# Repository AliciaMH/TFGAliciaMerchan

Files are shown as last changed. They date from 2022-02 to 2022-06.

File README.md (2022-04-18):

# TFGAliciaMerchan

# Carpeta: Excel Proyecto:

Aquí se encuentran todos los archivos de excel relacionados con el proyecto:
1) "CalculadoraErrorTiempo" : Para que las personas que quieran realizar el experimento puedan tener el valor exacto del error del tiempo para el recorrido que deseen y     a la velocidad que deseen. Sólo tendrán que introducir los parámetros iniciales (ángulo final, inicial y velocidad angular) y se calculará automáticamente el error.     Además, se proporciona como extra la información de la velocidad lineal a la que hará el experimento y la opción de obtener una gráfica como las anteriores en las       que según el ángulo inicial y la velocidad angular constante se puede obte-ner cómo variará el error según el ángulo final.

2) "VelocidadesAngulares_SimuladorGeologicoAlicia" : Aqui se recogen los datos principales del proyecto:
         Hojas:
         a) cálculos: contiene los cálculos para cada velocidad angular dada con las condiciones del motor usado, tiempo de espera necesario, etc
         b) Calculadora de error: es la misma que la del punto 1, por si se prefiere tenerlo todo junto en un único excel
         c) Velocidades medias: Cálculo de las velocidades lineales medias para cada velocidad angular (necesario para la hoja a)
         d) Linealización: Permite ver la correspondencia de los ángulos con la distancia recorrida por la bisagra especial. También hay una linealización que se comenta             en la memoria del TFG pero que al final no es necesaria ya que se realiza el cambio directo. 
         e) Error: Esta hoja se utilizó para la primera aproximación que se quería realizar, sin embargo, al final no fue la aproximación elegida asique se puede obviar.
         
# Carpeta: código final Arduino prueba casa
Aquí se encuentran el excel con los parámentros necesarios para hacer la simulación en casa con otro motor distinto, los csv con los vectores necesarios para el código de arduino y el propio código de arduino. El archivo de arduino que contiene un -10 en el nombre es el que se usó de prueba para establecer el sensor de inicio de carrera en un lugar distinto al 0.

# Carpeta: simulación SAM

Aquí se encuetra la simulación final con las medidas correspondientes del proyecto en un archivo .SAM para abrir en el programa y por otro lado el excel con los datos obtenidos de la simulación y la comparativa con los otros métodos.

# Carpeta: bisagra principal

Recoge algunos de los diseños para la bisagra principal realizados en freeCAD

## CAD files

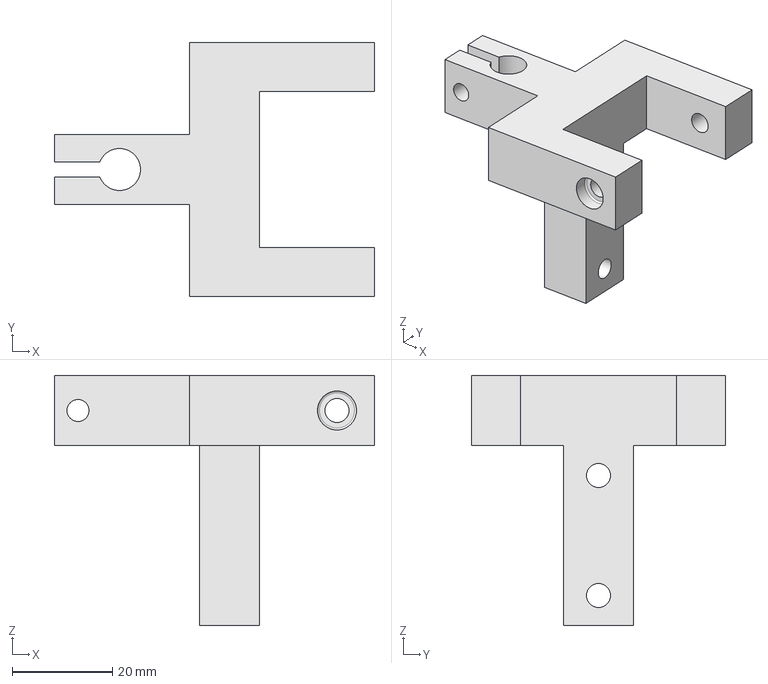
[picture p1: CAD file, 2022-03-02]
Bisagra Principal/ElementoUnionPerfil30mmEje8mm.FCStd
64.0 x 50.8 x 50.0 mm

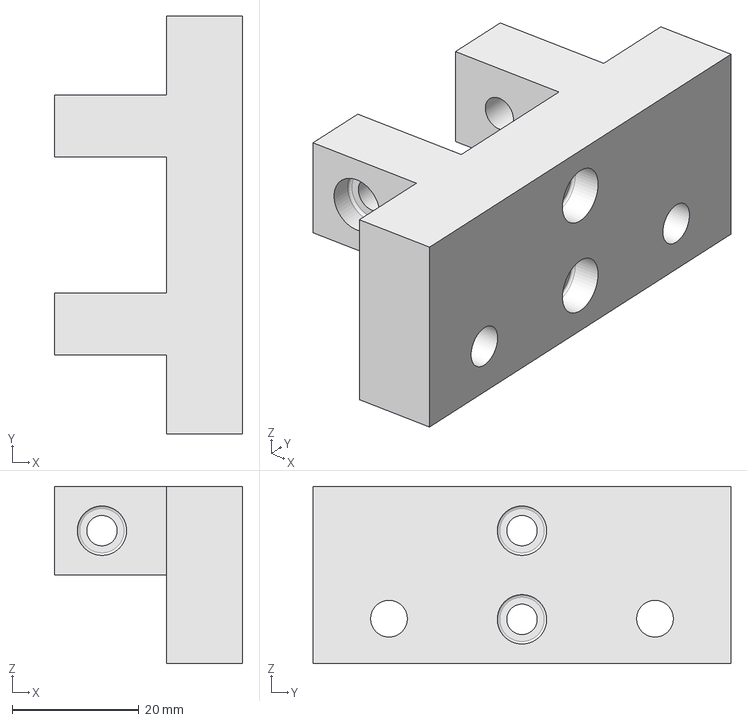
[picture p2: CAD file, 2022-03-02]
Bisagra Principal/ElementoUnionPerfil20mmPillowBlock8mm.FCStd
29.7 x 66.0 x 28.0 mm

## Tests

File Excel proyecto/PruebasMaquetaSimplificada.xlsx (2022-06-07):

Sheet: Hoja1
PRUEBA CON MAQUETA SIMPLIFICADA CASA
Prueba | a | b | c | d | e | f | g | h | i | j | k
θinicial (°) | 1 | 0 | 2 | 0 | 0 | 0 | 1.5 | 3 | -1 | 0 | 0
θfinal (°) | 3 | 3 | 6 | 1 | 5 | 1.5 | 7 | 6 | 4 | 8 | 7.5
ω (°/h) | 8 | 8.8 | 6 | 3 | 9.9 | 1.5 | 7 | 3 | 6.5 | 8.5 | 9
Avance
a_sim (mm) | 24.47 | 36.69 | 49.13 | 12.22 | 61.25 | 18.33 | 67.62 | 36.89 | 61.17 | 98.39 | 92.17
a_teo (mm) | 24.47 | 36.69 | 49.13 | 12.22 | 61.24 | 18.33 | 67.62 | 36.89 | 61.17 | 98.38 | 92.16
error (%) | 0.01 | 0.01 | 0.004070998209 | 0.02 | 0.01 | 0.00 | 0.001478874281 | 0.01 | 0.004391544475 | 0.01 | 0.01
Tiempo(h)
t_sim (h) | 0.243 | 0.321 | 0.640 | 0.292 | 0.481 | 0.906 | 0.768 | 0.958 | 0.746 | 0.906 | 0.796
t_aprox (h) | 0.242 | 0.330 | 0.648 | 0.323 | 0.490 | 0.968 | 0.765 | 0.974 | 0.745 | 0.917 | 0.811
t_teo (h) | 0.250 | 0.341 | 0.667 | 0.333 | 0.505 | 1.000 | 0.786 | 1 | 0.769 | 0.941 | 0.833
error (%) | -0.550 | 2.862 | 1.277 | 9.615 | 1.814 | 6.365 | -0.399 | 1.669 | -0.042 | 1.112 | 1.802
error absoluto | -0.001 | 0.009 | 0.008 | 0.031 | 0.009 | 0.062 | -0.003 | 0.016 | -0.0003153086918 | 0.010 | 0.015
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

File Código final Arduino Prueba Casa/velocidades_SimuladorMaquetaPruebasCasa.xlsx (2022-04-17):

 |  |  |  |  |  |  |  |  | TEORICO | EL QUE VAMOS A DAR
wdado(grados/h) | v (cm/h) | v (mm/h) | v (μm/s) | medio paso/s | s/medio paso | ms / medio paso | us / medio paso | t_mediomicropaso (ms) | t_mediomicropaso (us) | t_mediomicropaso (us) | t_espera (us)
0 | 0.0000 | 0 | 0 | 0 | 0 | 0.00 | 0.00 | 0.000 | 0.00 | 0 | 0.00
0.1 | 0.1263 | 1.262727836 | 0.351 | 0.140 | 7.127 | 7127.43 | 7127426.63 | 222.732 | 222732.08 | 100 | 7124226.63 | Pasos por vuelta = | 200 | VELOCIDAD MINIMA
0.2 | 0.2525 | 2.525455672 | 0.702 | 0.281 | 3.564 | 3563.71 | 3563713.31 | 111.366 | 111366.04 | 100 | 3560513.31 | Reduccion = | 1
0.3 | 0.3788 | 3.788183507 | 1.052 | 0.421 | 2.376 | 2375.81 | 2375808.88 | 74.244 | 74244.03 | 100 | 2372608.88 | Pasos / vuelta = | 200 | PPS1/2 = | 150
0.4 | 0.5051 | 5.050911343 | 1.403 | 0.561 | 1.782 | 1781.86 | 1781856.66 | 55.683 | 55683.02 | 100 | 1778656.66 | Avance / vuelta (mm) = | 1 | vmin (μm/s) = | 375.000
0.5 | 0.6314 | 6.313639179 | 1.754 | 0.702 | 1.425 | 1425.49 | 1425485.33 | 44.546 | 44546.42 | 100 | 1422285.33 | Avance / paso (mm) = | 0.005 | vmin (cm/h) = | 135.000
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

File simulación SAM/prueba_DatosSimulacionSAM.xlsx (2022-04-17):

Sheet: Datos sam maqueta actual(9 grad
Result listing SAM 6.1.46 . Mechanism: Modelo final
________________________________________________________________________ |  |  |  |  | unidades corregidas |  | velocidad lineal husillo |  | Distancia real considernado el 0 en 0 grados |  |  | Velocidad angular placa
Nr: | A(1) | Vy(2) | y(2) | AV(1) | A(1) | Vy(2) | Vy(2) | y(2) | Y_0(2) | Y_0(2) | AV(1) | AV(1) |  | Vy(2)_SAM | Vy(2)_Formula | Vy(2)_RadReal | Vy(2)_const | Error SAM/Formula
[-] | [deg] | [mm/s] | [mm] | [deg/s] | [deg] | [mm/s] | [cm/h] | [mm] | [mm] | [cm] | [deg/s] | [deg/h] |  | [cm/h] | [cm/h] | [cm/h] | [cm/h] | [cm/h]
0 | 0 | 27.15 | 300000 | 2.222 | 0 | 0.02715 | 9.7740 | 300 | 0 | 0 | 0.002222 | 7.9992 |  | 9.7740 | 9.7729 | 9.7738 | 9.93388853 | 0.0011
1 | 1000 | 27.16 | 312200 | 2.222 | 1 | 0.02716 | 9.7776 | 312.2 | 12.2 | 1.22 | 0.002222 | 7.9992 |  | 9.7776 | 9.7758 | 9.7753 | 9.93388853 | 0.0018
2 | 2000 | 27.18 | 324400 | 2.222 | 2 | 0.02718 | 9.7848 | 324.4 | 24.4 | 2.44 | 0.002222 | 7.9992 |  | 9.7848 | 9.7848 | 9.7798 | 9.93388853 | 1.595213334e-05
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

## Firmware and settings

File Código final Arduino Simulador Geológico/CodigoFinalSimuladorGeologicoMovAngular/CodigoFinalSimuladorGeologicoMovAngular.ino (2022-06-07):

//CÓDIGO FINAL ARDUINO PARA SIMULACIÓN GEOLÓGICA CON MOVIMIENTO ANGULAR//Falta cambiar los vectores y la sensibilidad

#include <TimerOne.h>       // Libreria del timer 1
#include <TimerThree.h>     // Libreria del timer 3
#include <TimerFour.h>      // Libreria del timer 4

#include <LiquidCrystal.h>  // Libreria de la pantalla LCD
LiquidCrystal lcd(16, 17, 23, 25, 27, 29);

//Pines de la shield
#define LCD_PINS_RS 16      // LCD control conectado a GADGETS3D  shield LCDRS
#define LCD_PINS_ENABLE 17  // LCD enable pin conectado a GADGETS3D shield LCDE
#define LCD_PINS_D4 23      // LCD signal pin, conectado a GADGETS3D shield LCD4
#define LCD_PINS_D5 25      // LCD signal pin, conectado a GADGETS3D shield LCD5
#define LCD_PINS_D6 27      // LCD signal pin, conectado a GADGETS3D shield LCD6
#define LCD_PINS_D7 29      // LCD signal pin, conectado a GADGETS3D shield LCD7
#define X_MIN_PIN 3         // PIN para el fin de carrera colocado al inicio del recorrido (1: presionado (true))
#define X_MAX_PIN 2         // PIN para el fin de carrera colocado al inicio del recorrido (1: presionado (true))

#define X_STEP_PIN 54       // PIN de los pasos del controlador DRV8825 del motor paso a paso
#define X_DIR_PIN 55        // PIN de la direccion del controlador DRV8825 del motor paso a paso
#define X_ENABLE_PIN 38     // PIN del enable del controlador DRV8825 del motor paso a paso

#define BTN_EN1 31          // Encoder, conectado a GADGETS3D shield S_E1
#define BTN_EN2 33          // Encoder, cconectado a GADGETS3D shield S_E2
#define BTN_ENC 35          // Encoder Click, connected to Gadgets3D shield S_EC

// VARIABLES MEDIDA POSICION

bool fc_inic_X = true;      // Valor del final de carrera situacion al inicio del experimento
bool fc_fin_X = true;       // Valor del final de carrera situacion al final del experimento

const float L = 254.78;     // Corresponde a la distancia máxima, es decir, cuando el ángulo es 20 grados
float LMin = -123.429;      // Corresponde a la distancia mínima, es decir, cuando el ángulo es -10 grados. Corresponde además al lugar dónde irá colocado el sensor inicio de carrera
int Lb = 700;               // Longitud entre la bisagra especial y la bisagra principal
const float pi = 3.14159265;// pi number
int AMax = 20;              // Ángulo máximo que se puede llevar a cabo
int AMin = -10;             // Ángulo minimo que se puede llevar a cabo

// VARIABLES MEDIDA TIEMPO 

int horas = 0;              // Variable que cuenta las horas del experimento
int minutos = 0;            // Variable que cuenta los minutos del experimento
volatile int segundos = 0;  // Variable que cuenta los segundos del experimento

// VARIABLES MOVIMIENTO MOTOR

unsigned long t_mediomicropaso = 0;   // Variable en la que introducimo el tiempo de cada medio micropaso
unsigned long t_mediopaso = 0;        // Variable en la que introducimo el tiempo de cada medio paso
int v = 1;                            // Velocidad del sistema
int Vmax = 100;                        // Posición 100 de los vectores de medio paso y micro paso(1000 cm/h)
int posicion = 0;                     //Cogerá v si estoy en el experimento normal o Vmax si estoy yendo a 0
volatile int nivel = LOW;             // Nivel del motor paso a paso
unsigned long micropasos = 0;         // Numero de micropasos dados
unsigned long n_mediospasos = 0;      // Numero de medios pasos cuando el experimento empieza en 0 mm
volatile int n_mediospasos2 = 0;      // Numero de medios pasos cuando el experimento no empieza en 0 mm
float avance_mediospasos = 0;         // Avance a partir de los medios pasos dados por el motor conocido su avance por cada medio paso cuando el experimento empieza en 0 mm
float avance_mediospasos2 = 0;        // Avance a partir de los medios pasos dados por el motor conocido su avance por cada medio paso cuando el experimento no empieza en 0 mm
float di_X, df_X = 0;                 // Distancia inicial y final que queremos en el experimento. Lo he cambiado por float para que pueda tener decimales
float ang_i, ang_f = 0;               // Ánulos iniciales, será lo que elija el usuario en este experimento
float rad, radf, radMin=0;            // Variable para pasar el número de grados a radianes para poder utilizar la tangente

// El siguiente vector muestra los tiempos de cada medio micropaso dependiendo de la velocidad seleccionado. Este vector se encuentra en un .csv en el GitHub del autor del trabajo
// El último elemento corresponde a la mayor velocidad que puede alcanzar para que pueda ir hasta el ángulo inicial indicado a una velocidad mayor
float vectort_mediomicropaso[] = {0,78,78,78,78,78,78,78,78,78,78,78,78,78,78,78,78,78,78,78,78,78,78,78,78,78,78,78,78,78,78,78,78,78,78,78,78,78,78,78,78,78,78,78,78,78,78,78,78,78,78,78,78,78,78,78,78,78,76.80416624,75.50240071,74.24402737,73.02691216,71.84905874,70.70859749,69.60377566,68.53294834,67.49457033,66.48718869,65.50943591,64.5600238,63.63773774,62.74143158,61.87002281,61.02248825,60.19786003,59.39522189,58.61370582,57.85248886,57.11079028,56.38786889,55.68302053,54.99557583,54.32489807,53.67038123,53.03144812,52.40754873,51.79815863,51.20277749,50.62092775,50.05215328,49.49601824,48.95210596,48.42001785,47.89937249,47.3898047,46.89096465,46.4025171,45.92414064,45.45552696,44.99638022,28.39};

// El siguiente vector muestra los tiempos de cada medio paso dependiendo de la velocidad seleccionado. Este vector se encuentra en un .csv en el GitHub del autor del trabajo
// El último elemento corresponde a la mayor velocidad que puede alcanzar para que pueda ir hasta el ángulo inicial indicado a una velocidad mayor
float vectort_mediopaso[] = {0,142548.5325,71274.26627,47516.17751,35637.13314,28509.70651,23758.08876,20364.07608,17818.56657,15838.72584,14254.85325,12958.9575,11879.04438,10965.27173,10182.03804,9503.235503,8909.283284,8385.207797,7919.362919,7502.554344,7127.426627,6788.025359,6479.478752,6197.762285,5939.522189,5701.941302,5482.635867,5279.575279,5091.019019,4915.466639,4751.617751,4598.339759,4454.641642,4319.652501,4192.603898,4072.815216,3959.68146,3852.663042,3751.277172,3655.090578,3563.713314,3476.793477,3394.01268,3315.082152,3239.739376,3167.745168,3098.881142,3032.947501,2969.761095,2909.153725,2850.970651,2795.069266,2741.317934,2689.594954,2639.78764,2591.791501,2545.50951,2500.851448,2457.73332,2416.076823,2375.808876,2336.861189,2299.16988,2262.67512,2227.320821,2193.054347,2159.826251,2127.590038,2096.301949,2065.920762,2036.407608,2007.72581,1979.84073,1952.719624,1926.331521,1900.647101,1875.638586,1851.279643,1827.545289,1804.411804,1781.856657,1759.858426,1738.396738,1717.452199,1697.00634,1677.041559,1657.541076,1638.48888,1619.869688,1601.668905,1583.872584,1566.467391,1549.440571,1532.77992,1516.47375,1500.510869,1484.880547,1469.5725,1454.576863,1439.884167,908.63};


// VARIABLES MAQUINA DE ESTADOS

int inicio = 0;                       // Variable que inicia el experimento cuando comienza en el sensor de principio de carrera
int inicio_experimento = 0;           // Variable que inicia el experimento cuando comienza en di_X mm
int inicio_contadortiempo = 0;       // Variable que inicia el experimento cuando no comienza en 0 mm
int fin = 0;                          // Variable que para el experimento cuando llega al final de carrera 
int volatile estado = 0;              // Variables del estado


// VARIABLES LCD

int fila, columna = 0;                                             // Variable de fila y columna en la pantalla lcd
bool btn_en1, btn_en2, btn_enc, btn_en1_prev, btn_en2_prev ;       // Variables de lectura directa del codificador giratorio mecanico
bool direccion = false;                                            // Direccion del codificador
bool derecha, izquierda, pulsador = false;                         // Variables de lectura del codificador interpretadas
int i = 0;                                                         // Contador de pulsos

// SIGNOS CREADOS

byte empty[8] =
{
  B00000,
  B00100,
  B01010,
  B10001,
  B10001,
  B01010,
  B00100,
};
byte full[8] =
{
  B00000,
  B00100,
  B01110,
  B11111,
  B11111,
  B01110,
  B00100,
};
byte micro[8] =
{
  B00000,
  B10001,
  B10001,
  B11011,
  B10101,
  B10000,
  B10000,
};
byte arrow[8] =
{
  B00000,
  B00001,
  B00001,
  B00001,
  B01001,
  B11111,
  B01000,
};

void setup() {

  pinMode(BTN_EN1, INPUT_PULLUP);     // Encoder 1
  pinMode(BTN_EN2, INPUT_PULLUP);     // Encoder 2
  pinMode(BTN_ENC, INPUT_PULLUP);     // Encoder Swith
  
  pinMode(X_MIN_PIN, INPUT_PULLUP);   // Fin de carrera inicio  
  pinMode(X_MAX_PIN, INPUT_PULLUP);   // Fin de carrera final           

  lcd.begin(20, 4);   // 20 columnas y 4 filas

  pinMode(X_STEP_PIN , OUTPUT);
  pinMode(X_DIR_PIN , OUTPUT);
  pinMode(X_ENABLE_PIN , OUTPUT);

  btn_en1 , btn_en1_prev = digitalRead(BTN_EN1);
  btn_en2 , btn_en2_prev = digitalRead(BTN_EN2);
  btn_enc = digitalRead(BTN_ENC);

  lcd.createChar(0, empty);   // 0: numero de carácter; empty: matriz que contiene los pixeles del carácter
  lcd.createChar(1, full);    // 1: numero de carácter; full: matriz que contiene los pixeles del carácter
  lcd.createChar(2, micro);   // 2: numero de carácter; micro: matriz que contiene los pixeles del carácter
  lcd.createChar(3, arrow);   // 3: número de carácter; arrow: matriz que contiene los pixeles del carácter
 
  digitalWrite(X_ENABLE_PIN , LOW);         // Habilitación a nivel bajo del motor paso a paso

  Timer3.initialize(1000000);              // Inicialización de la interrupcion del contador de segundos
  Timer3.attachInterrupt(Temporizador);    // Función de la interrupcion del contador de segundos
  
}

////////////////// PROCESOS ENCODER /////////////////////

void leer_encoder()
{
  btn_en1 = digitalRead(BTN_EN1);
  btn_en2 = digitalRead(BTN_EN2);
  digitalWrite(X_DIR_PIN, direccion);

  if (btn_en1 != btn_en1_prev || btn_en2 != btn_en2_prev)
  {
    if (btn_en2 == false & btn_en1 == false & btn_en2_prev == true & btn_en1_prev == false)
    {
      derecha = true;
      izquierda = false;
    }
    else if ( btn_en2 == false & btn_en1 == false & btn_en2_prev == false & btn_en1_prev == true )
    {
      derecha = false;
      izquierda = true;
    }
    else
    {
      derecha = false;
      izquierda = false;
    }
  }
  else
  {
    derecha = false;
    izquierda = false;
  }
  btn_en1_prev = btn_en1;
  btn_en2_prev = btn_en2;
}

void leer_pulso()
{
  btn_enc = digitalRead(BTN_ENC);

  if (btn_enc == false) //Detector de flanco del pulsador
  {
    i++;
  }
  if (i >= 80)
  {
    pulsador = true;
    i = 0;
    delay(200);
  }
  else
  {
    pulsador = false;
  }
}

//////////////////////// ESTADO 0 /////////////////////////

void pantalla_inicio()
{
  lcd.clear();
  lcd.setCursor(2, 0);    // posiciona el cursor en la columna 1 fila 0
  lcd.print("ENSAYO DE MODELO");
  lcd.setCursor(3, 1);    // posiciona el cursor en la columna 1 fila 1
  lcd.print("ANALOGO SIMPLE");

  lcd.setCursor(0, 3);    // posiciona el cursor en la columna 1 fila 3
  lcd.print("Iniciar Experimento");
  
}


//////////////// ESTADO 1 ////////////////

void menu()
{
  fila, columna = 0;
  di_X = 0;
  df_X = 0;
  ang_i = 0;
  ang_f = 0;
  v = 1;

  lcd.setCursor(1, 0);
  lcd.print("ang.ini");
  lcd.setCursor(12, 0);
  lcd.print(ang_i);
  lcd.setCursor(18, 0);
  lcd.print(char(223));//para que me aparezcan los grados de unidad de medida
  lcd.setCursor(1, 1);
  lcd.print("ang.fin");
  lcd.setCursor(12, 1);
  lcd.print(ang_f);
  lcd.setCursor(18, 1);
  lcd.print(char(223));
  lcd.setCursor(1, 2);
  lcd.print("velocidad");
  lcd.setCursor(12, 2);
  lcd.print(v);
  lcd.setCursor(16, 2);
  lcd.print(char(223));
  lcd.setCursor(17, 2);
  lcd.print("/h");
  lcd.setCursor(1, 3);
  lcd.print("Iniciar experimento");
  lcd.setCursor(0, 0);
  lcd.write(byte(0));
  lcd.setCursor(0, 1);
  lcd.write(byte(0));
  lcd.setCursor(0, 2);
  lcd.write(byte(0));
  lcd.setCursor(0, 3);
  lcd.write(byte(0));
  lcd.setCursor(0, fila);
  lcd.write(byte(1));
}

//////////////// ESTADO 2 ////////////////

void DefinicionDeVariables()
{
  switch (fila) // fila es la variable vertical de la pantalla, indica que variable se esta manipulando
  {
    case 0: // modificar el ángulo inicial
      if (pulsador == true  and columna < 2) // columna es una variable que avanza en horizontal por la pantalla, cuando vale 0 podemos cambia en vertical con derecha o izquierda, cuando no aumentamos la variable con la que estemos trabajando
      {
        columna++;
      }
      else if (pulsador == true and columna == 2) //hay 3 opciones
      {
        columna = 0;
      }
      switch (columna)
      {
        case 0: //opción 1: seleccionar variable
          if (derecha == true )
          {
            fila = 1;
            lcd.setCursor(0, 0);
            lcd.write(byte(0));
            lcd.setCursor(0, 1);
            lcd.write(byte(1));
            lcd.setCursor(0, 2);
            lcd.write(byte(0));
            lcd.setCursor(0, 3);
            lcd.write(byte(0));
          }
          else if (izquierda == true)
          {
            fila = 3;
            lcd.setCursor(0, 0);
            lcd.write(byte(0));
            lcd.setCursor(0, 1);
            lcd.write(byte(0));
            lcd.setCursor(0, 2);
            lcd.write(byte(0));
            lcd.setCursor(0, 3);
            lcd.write(byte(1));
          }
          break;
        case 1: //opción 2: ir sumando y restando de 0.1 en 0.1
          if (derecha == true and ang_i +0.1 < AMax)
          {
            ang_i = ang_i + 0.1;
            lcd.setCursor(12, 0);
            lcd.print("   ");
            lcd.setCursor(12, 0);
            lcd.print(ang_i);
          }
          else if (izquierda == true and ang_i -0.1 > AMin)
          {
            ang_i = ang_i - 0.1;
            lcd.setCursor(12, 0);
            lcd.print("   ");
            lcd.setCursor(12, 0);
            lcd.print(ang_i);
          }
          break;
          
        default://opción 3: ir sumando y restando de 1 en 1
          if (derecha == true and ang_i +1 < AMax)
          {
            ang_i = ang_i + 1;
            lcd.setCursor(12, 0);
            lcd.print("   ");
            lcd.setCursor(12, 0);
            lcd.print(ang_i);
          }
          else if (izquierda == true and ang_i -1 > AMin)
          {
            ang_i = ang_i - 1;
            //rad= (ang_i * pi)/180;
            //di_X= Lb*tan(rad);
            lcd.setCursor(12, 0);
            lcd.print("   ");
            lcd.setCursor(12, 0);
            lcd.print(ang_i); 
          }
          break;
          rad= (ang_i * pi)/180;
          di_X= Lb*tan(rad);
        
      }
      break;
    case 1: // modificar el ángulo final
      if (pulsador == true  and columna < 2) // columna es una variable que avanza en horizontal por la pantalla, cuando vale 0 podemos cambia en vertical con derecha o izquierda, cuando no aumentamos la variable con la que estemos trabajando
      {
        columna++;
      }
      else if (pulsador == true and columna == 2)
      {
        columna = 0;
      }
      switch (columna)
      {
        case 0: //opción 1: seleccionar variable
          if (derecha == true )
          {
            fila = 2;
            lcd.setCursor(0, 0);
            lcd.write(byte(0));
            lcd.setCursor(0, 1);
            lcd.write(byte(0));
            lcd.setCursor(0, 2);
            lcd.write(byte(1));
            lcd.setCursor(0, 3);
            lcd.write(byte(0));
          }
          else if (izquierda == true)
          {
            fila = 0;
            lcd.setCursor(0, 0);
            lcd.write(byte(1));
            lcd.setCursor(0, 1);
            lcd.write(byte(0));
            lcd.setCursor(0, 2);
            lcd.write(byte(0));
            lcd.setCursor(0, 3);
            lcd.write(byte(0));
          }
          break;
        case 1: //opción 2: ir sumando y restando de 0.1 en 0.1
          if (derecha == true and ang_f + 0.1 < AMax)
          {
            ang_f = ang_f + 0.1;
            lcd.setCursor(12, 1);
            lcd.print("   ");
            lcd.setCursor(12, 1);
            lcd.print(ang_f);
          }
          else if (izquierda == true and ang_f -0.1 > AMin)
          {
            ang_f = ang_f - 0.1;
            //radf= (ang_f * pi)/180;
            //df_X= Lb*tan(radf);
            lcd.setCursor(12, 1);
            lcd.print("   ");
            lcd.setCursor(12, 1);
            lcd.print(ang_f);
          }
          break;
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
void loop() {// código que repite continuamente según el estado en el que esté
  
  switch (estado){//Máquina de estados
    case 0:
      pantalla_inicio();
      estado = 1;
      break;
            
    case 1:
      leer_pulso();
  
      if (pulsador == true) { 
        lcd.clear();
        menu();
        estado = 2;
      }
      
      break;

    case 2:
      leer_pulso();
      leer_encoder();
      DefinicionDeVariables();
      break;
   
    case 3: 
      experimento();
      break;    
  }
  
}

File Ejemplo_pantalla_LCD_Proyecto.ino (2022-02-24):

#include <LiquidCrystal.h>
LiquidCrystal lcd(12,11,5,4,3,2);

const int switchPin = 6; 
int switchState = 0;
int prevSwitchState = 0;
int reply;
float df_X = 0;                   // Distancia inicial y final que queremos en el experimento
int Angulofinal = 0;   // Ánulos iniciales, será lo que elija el usuario en este experimento
const float pi = 3.14159265;  // pi number
float rad = 0;
unsigned long tiempo1=0;
unsigned long tiempo2=0;
unsigned long diferenciatiempo=0;

void setup() {
  // put your setup code here, to run once:
  lcd.begin(16,2);
  pinMode(switchPin, INPUT);
  lcd.print("Para el");
  lcd.setCursor(0,1);
  lcd.print("Angulo dado");

}

void loop() {
  // put your main code here, to run repeatedly:
  switchState = digitalRead(switchPin);

  if (switchState != prevSwitchState){
    if (switchState == LOW) {
      reply = random(8);

      lcd.clear();
      lcd.setCursor(0,0);
      lcd.print("La distancia es:");
      lcd.setCursor(0,1);

      switch(reply){
        case 0:
//        AnguloFinal=reply;
        df_X= 700*tan(reply);
        lcd.print(df_X);
        break;
        case 1:
//        AnguloFinal=reply;
        tiempo1 = millis();
        rad= (reply * pi)/180;
        df_X= 700*tan(rad);
        tiempo2= millis();
        lcd.print(df_X);
        diferenciatiempo= tiempo1-tiempo2;
        lcd.setCursor(9,1);
        lcd.print(diferenciatiempo);
        break;
        case 2:
//        AnguloFinal=reply;
        tiempo1 = millis();
        rad= (reply * pi)/180;
        df_X= 700*tan(rad);
        tiempo2= millis();
        lcd.print(df_X);
        diferenciatiempo= tiempo1-tiempo2;
        lcd.setCursor(9,1);
        lcd.print(diferenciatiempo);
        break;
        case 4:
        tiempo1 = millis();
        rad= (reply * pi)/180;
        df_X= 700*tan(rad);
        tiempo2= millis();
        lcd.print(df_X);
        diferenciatiempo= tiempo1-tiempo2;
        lcd.setCursor(9,1);
        lcd.print(diferenciatiempo);
        break;
        case 5:
        tiempo1 = millis();
        rad= (reply * pi)/180;
        df_X= 700*tan(rad);
        tiempo2= millis();
        lcd.print(df_X);
        diferenciatiempo= tiempo1-tiempo2;
        lcd.setCursor(9,1);
        lcd.print(diferenciatiempo);
        break;
        case 6:
        tiempo1 = millis();
        rad= (reply * pi)/180;
        df_X= 700*tan(rad);
        tiempo2= millis();
        lcd.print(df_X);
        diferenciatiempo= tiempo1-tiempo2;
        lcd.setCursor(9,1);
        lcd.print(diferenciatiempo);
        break;
        case 7:
        tiempo1 = millis();
        rad= (reply * pi)/180;
        df_X= 700*tan(rad);
        tiempo2= millis();
        lcd.print(df_X);
        diferenciatiempo= tiempo1-tiempo2;
        lcd.setCursor(9,1);
        lcd.print(diferenciatiempo);
        break;
        
      }
    }
  }
 prevSwitchState = switchState;
}
